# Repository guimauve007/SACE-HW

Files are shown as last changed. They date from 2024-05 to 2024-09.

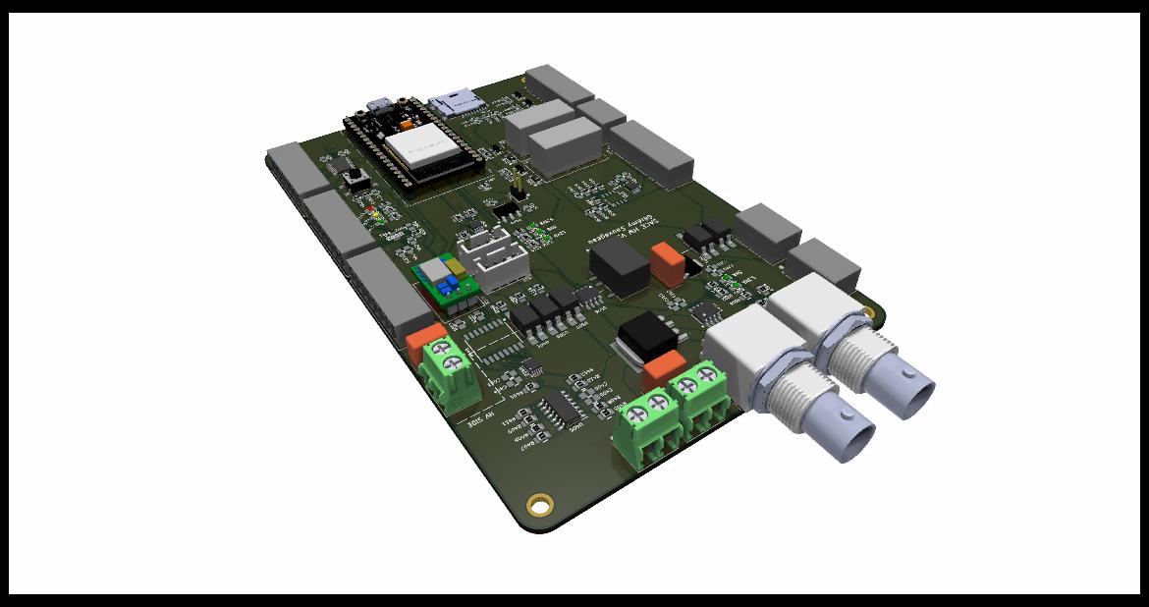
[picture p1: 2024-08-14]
carte_controle/V1/assets/SACE-HW(2).jpg

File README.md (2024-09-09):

# SACE-HW
Répertoire contenant 2 cartes pour machine SACE:

## Getting started
- Installer la dernière version de KiCad ici: https://www.kicad.org/download/
- Cloner ce répertoire sur votre ordinateur local:

```
git clone https://github.com/guimauve007/SACE-HW.git
```

## carte_controle (V1)
Module de contrôle versatile avec les fonctionnalités suivantes:
- 2 connecteurs BNC pour lecture de tension & de courant des électrodes (à l'oscilloscope)
- 8 GPIO/ADC 12 bits 5V
- 2 sorties 0-5V analog (DAC)
- 2 sorties 0-10V analog (DAC)
- 8 sorties 5V haute vitesse (pour stepper drive)
- 2 relais NO 125VAC-10Amp
- 4 Mosfet Open Drain pour load 12V 5.7Amp Max
- Lecture de tension + courant des électrodes jusqu'à 200kSPS avec résolution 12 bits
- Possibilité d'enregistrer un log de données via carte SD
- Interface web utilisateur avec communication MQTT via ESP32
- Connecteurs I2C (x2) pour accessoires auxiliaires  

## interface_piezzos (V1)
- Amplificateur de signal via OP-Amp en mode comparateur (sortie 0-5V)

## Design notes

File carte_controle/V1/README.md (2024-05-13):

# SACE-HW

Répertoire HW du module d'acquisition et d'alimentation de la SACE hybride 3 axes

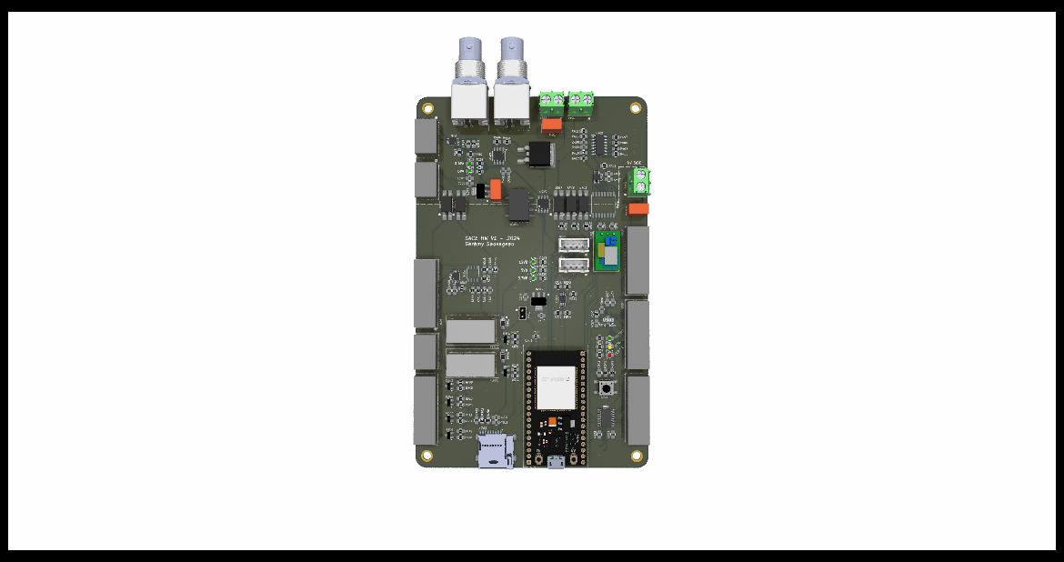
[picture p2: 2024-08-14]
carte_controle/V1/assets/SACE-HW.jpg

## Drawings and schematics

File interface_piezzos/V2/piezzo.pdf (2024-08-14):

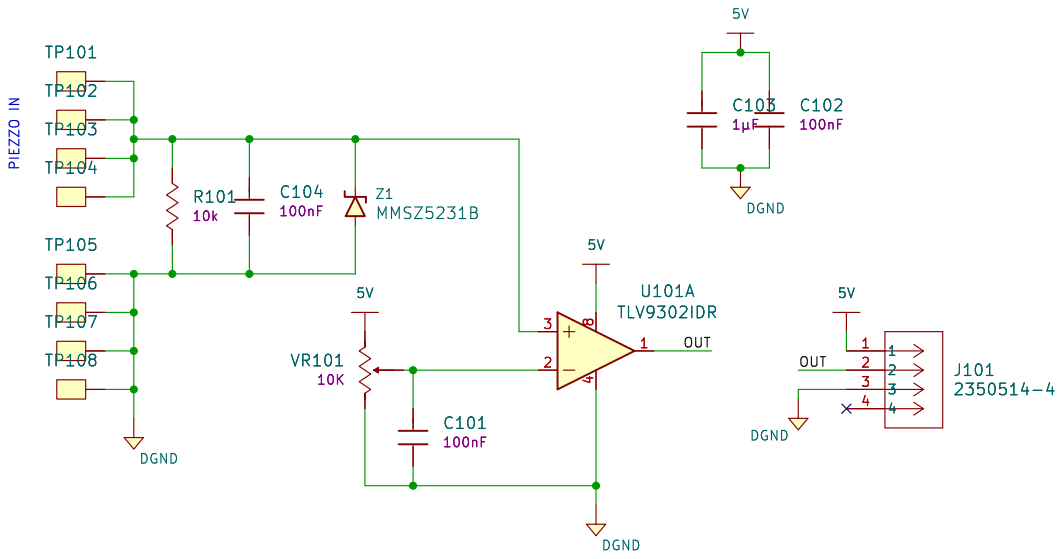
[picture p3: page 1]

File: piezzo.kicad_sch Sheet: / þÿGérémy Sauvageau

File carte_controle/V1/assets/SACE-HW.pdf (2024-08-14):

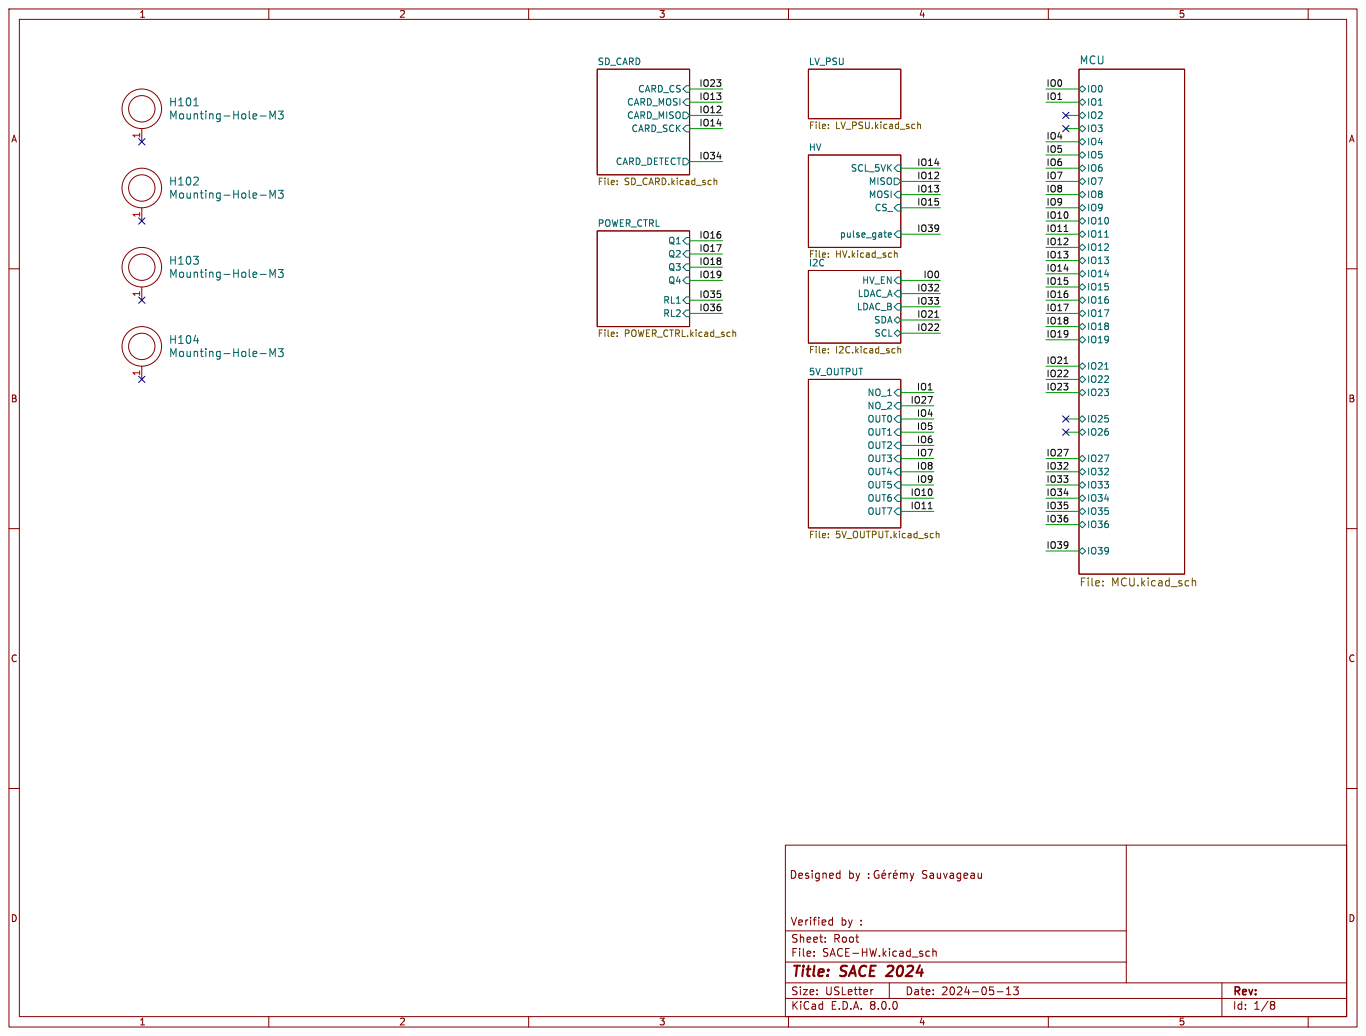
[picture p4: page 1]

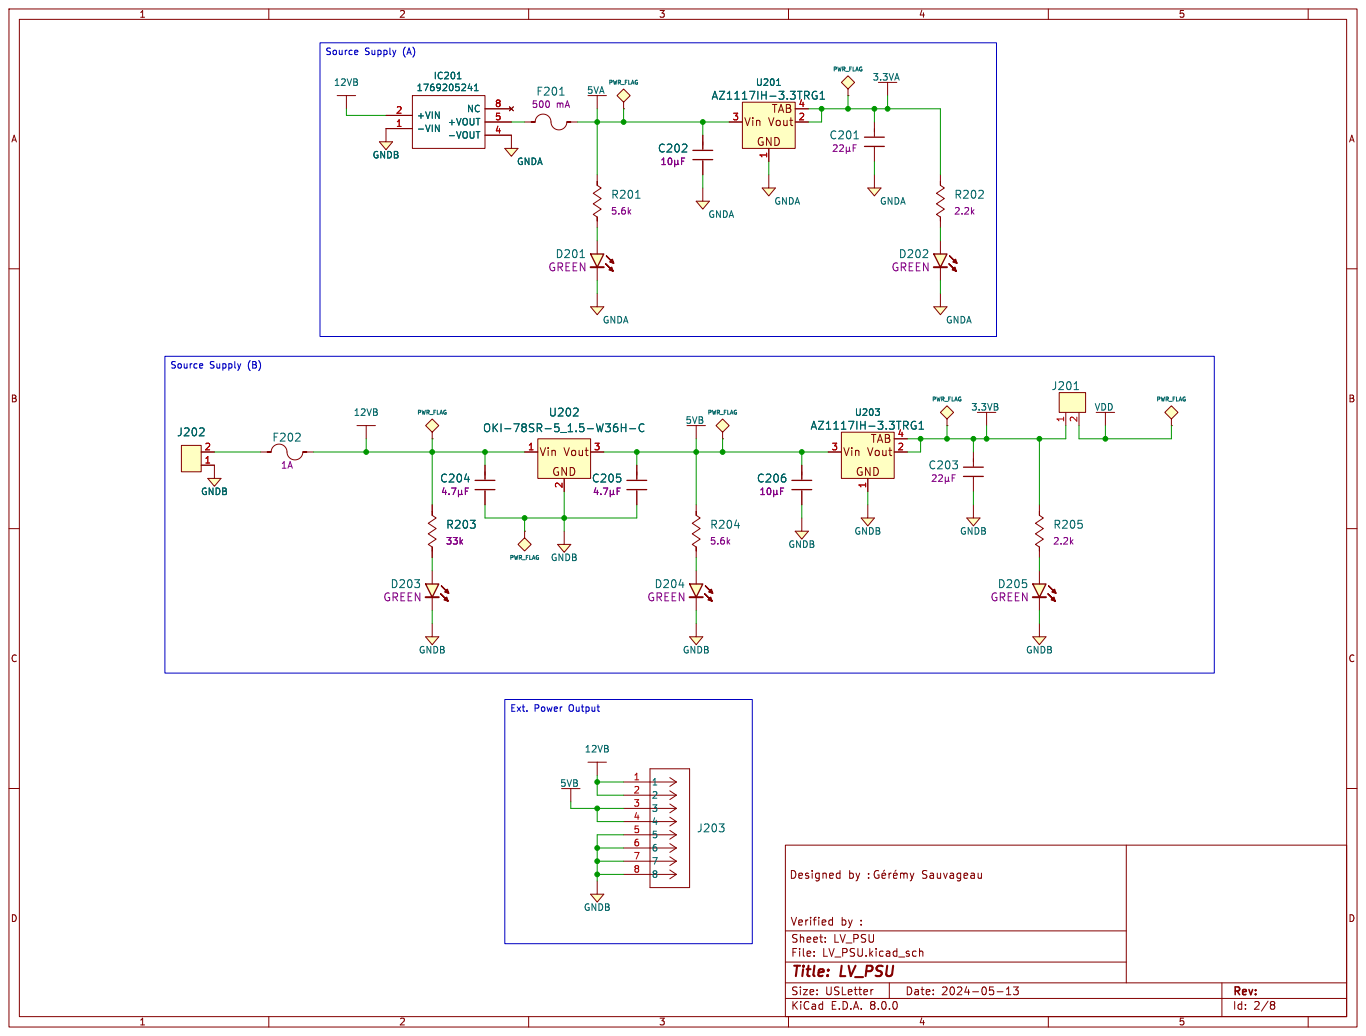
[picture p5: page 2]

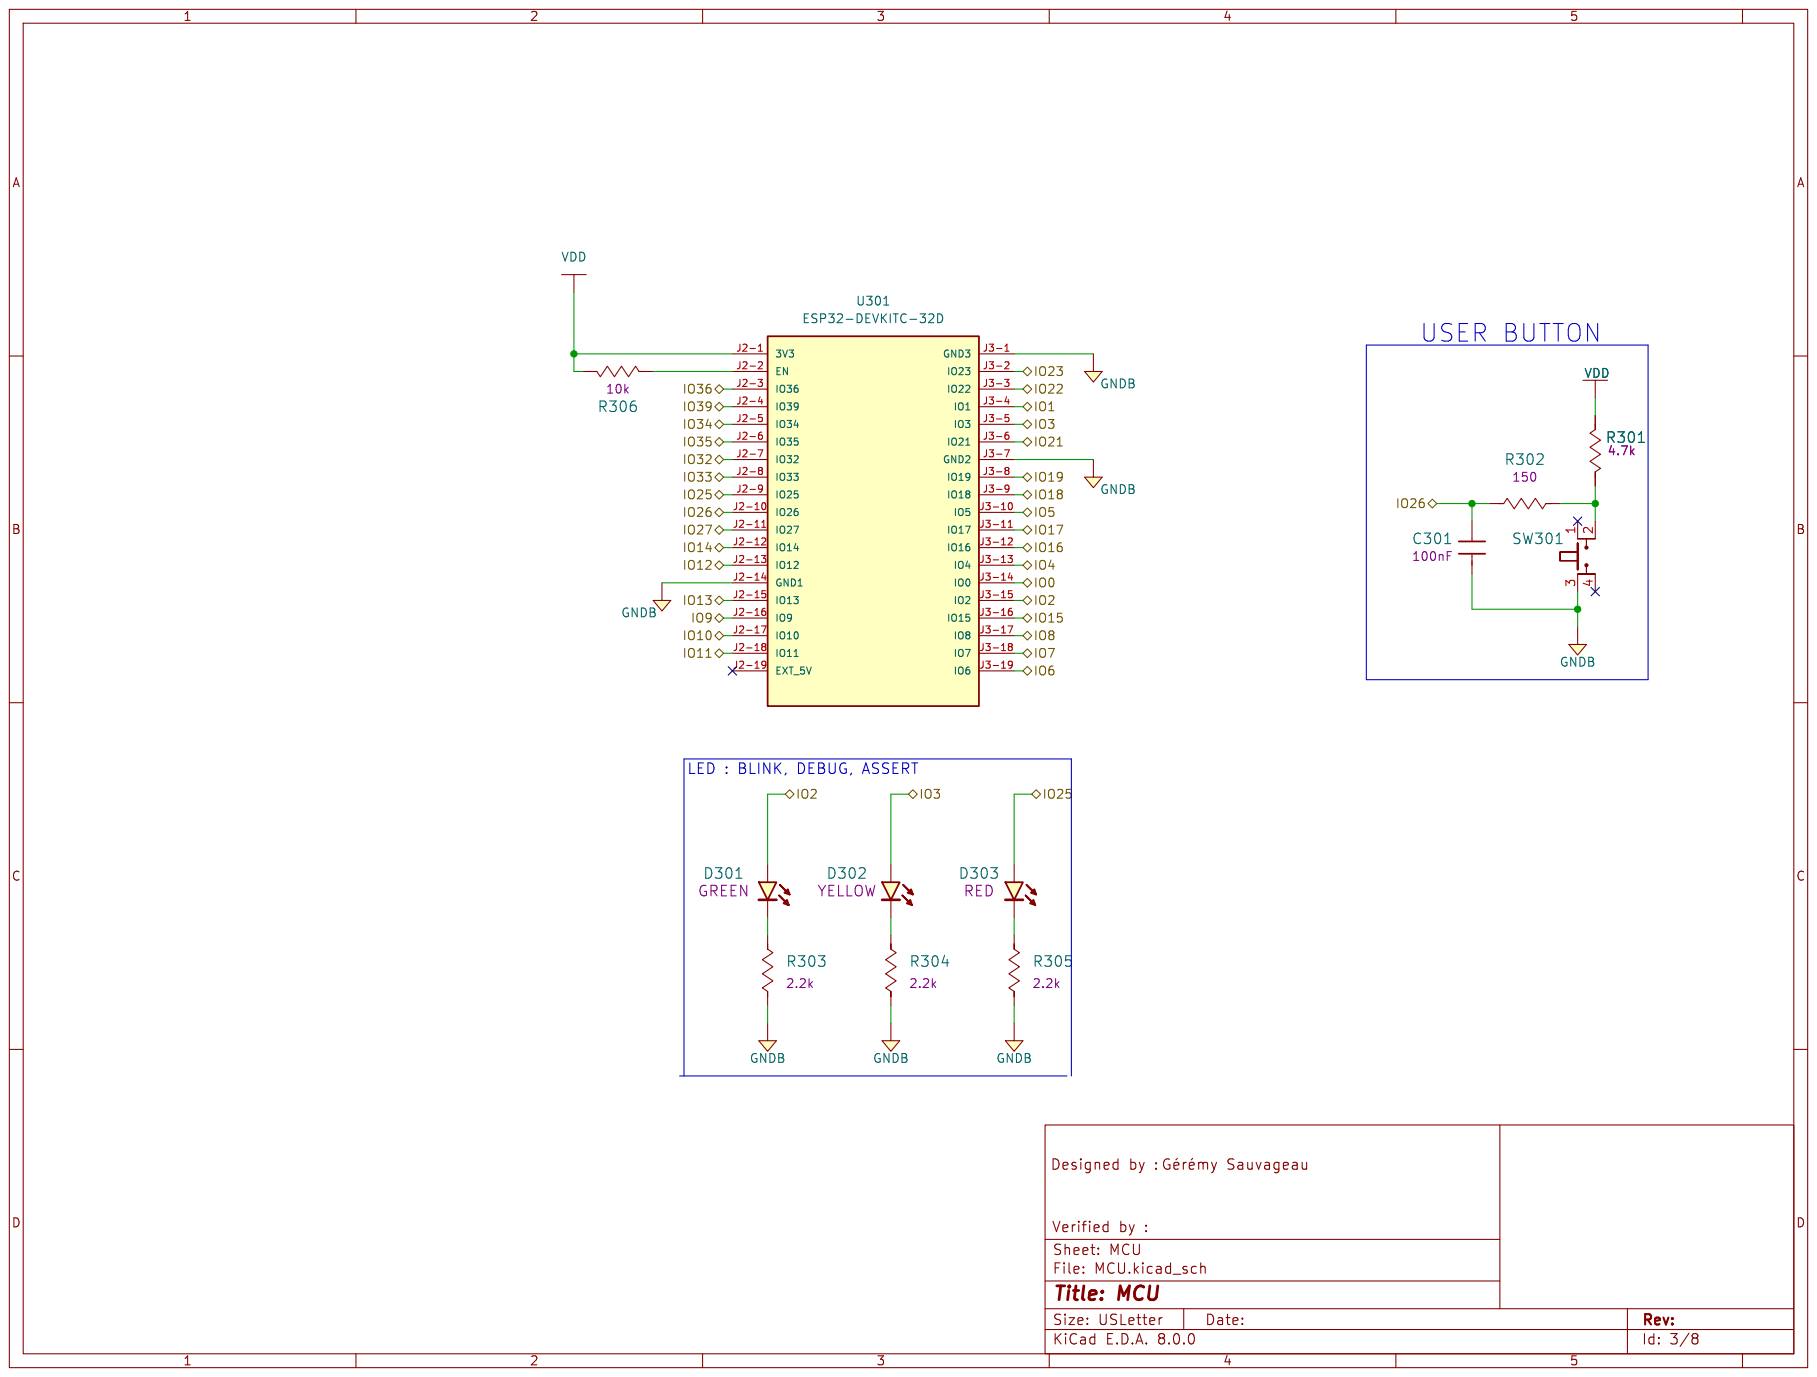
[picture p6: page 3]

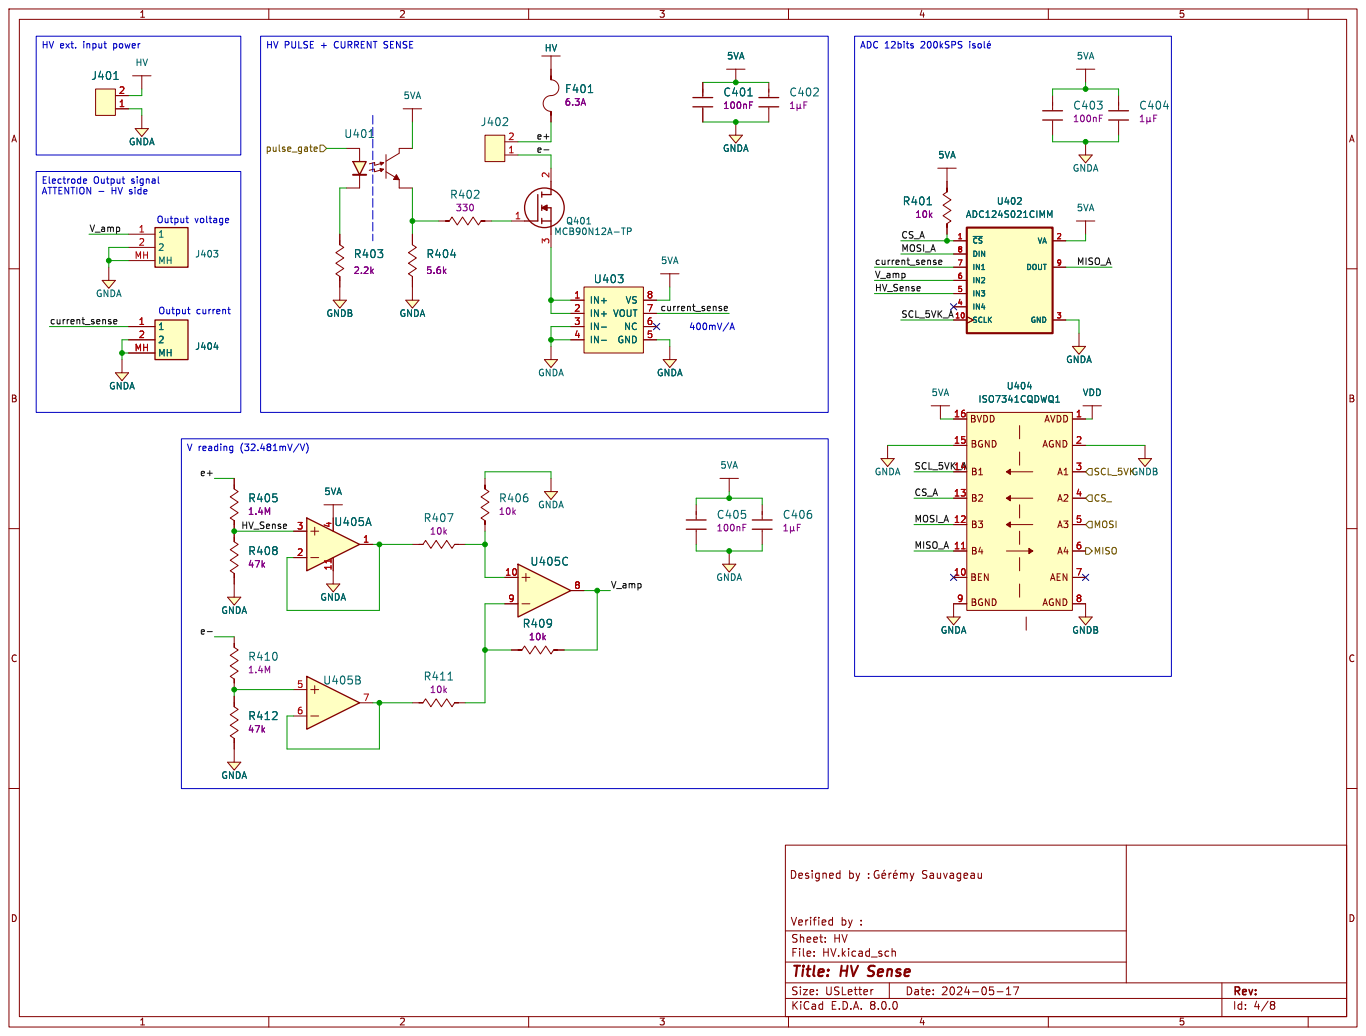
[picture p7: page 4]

Id: 4/8 Title: HV Sense

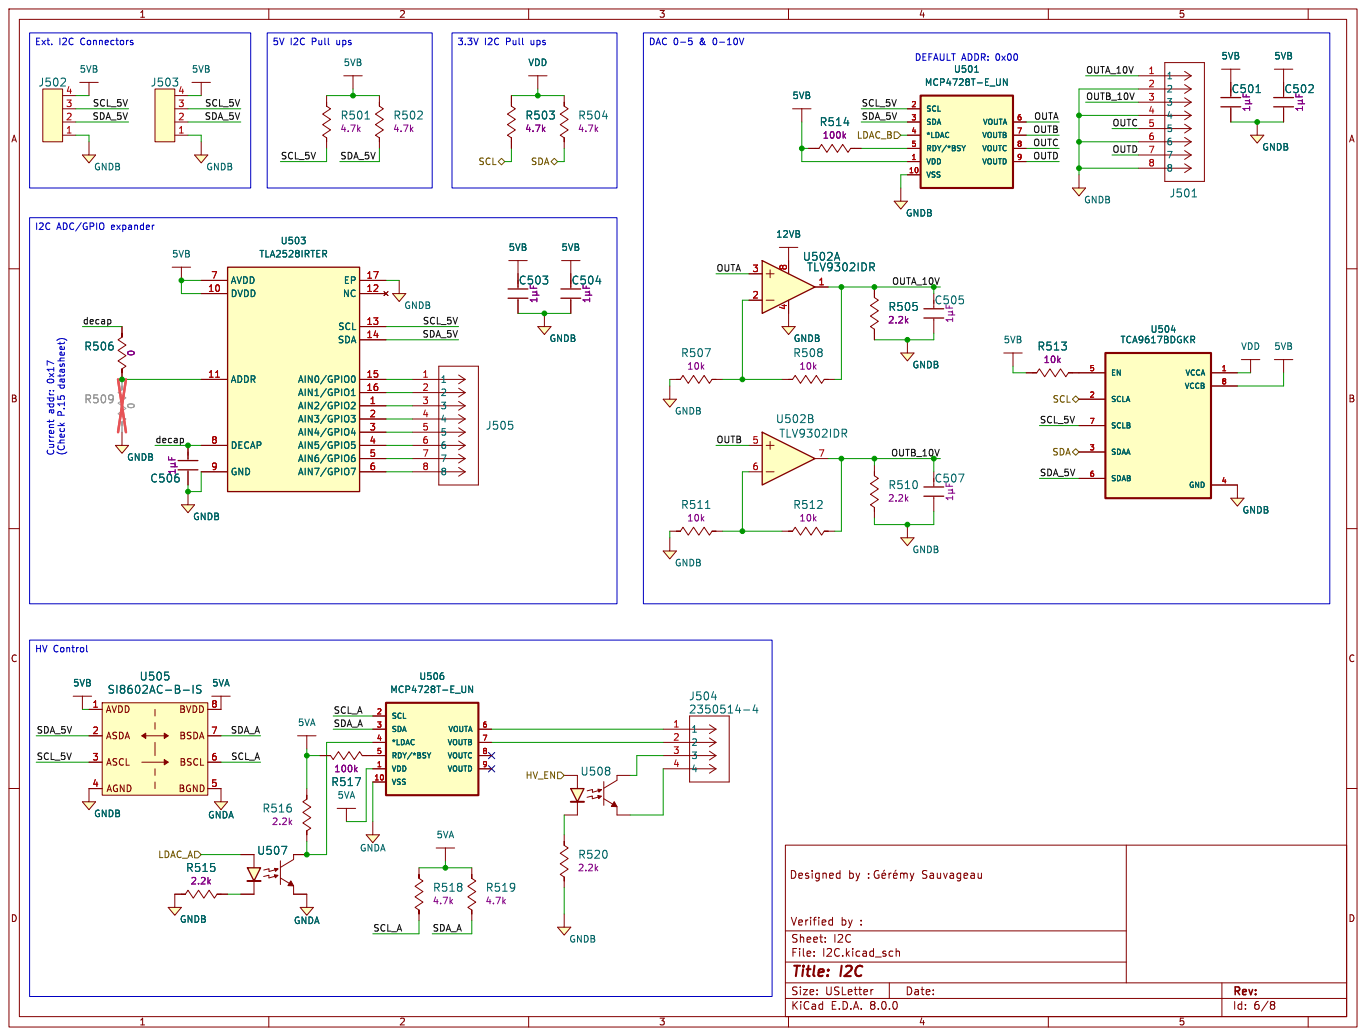
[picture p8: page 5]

I2C ADC/GPIO expander HV Control

SDA_5V Current addr: 0x17 (Check P.15 datasheet)

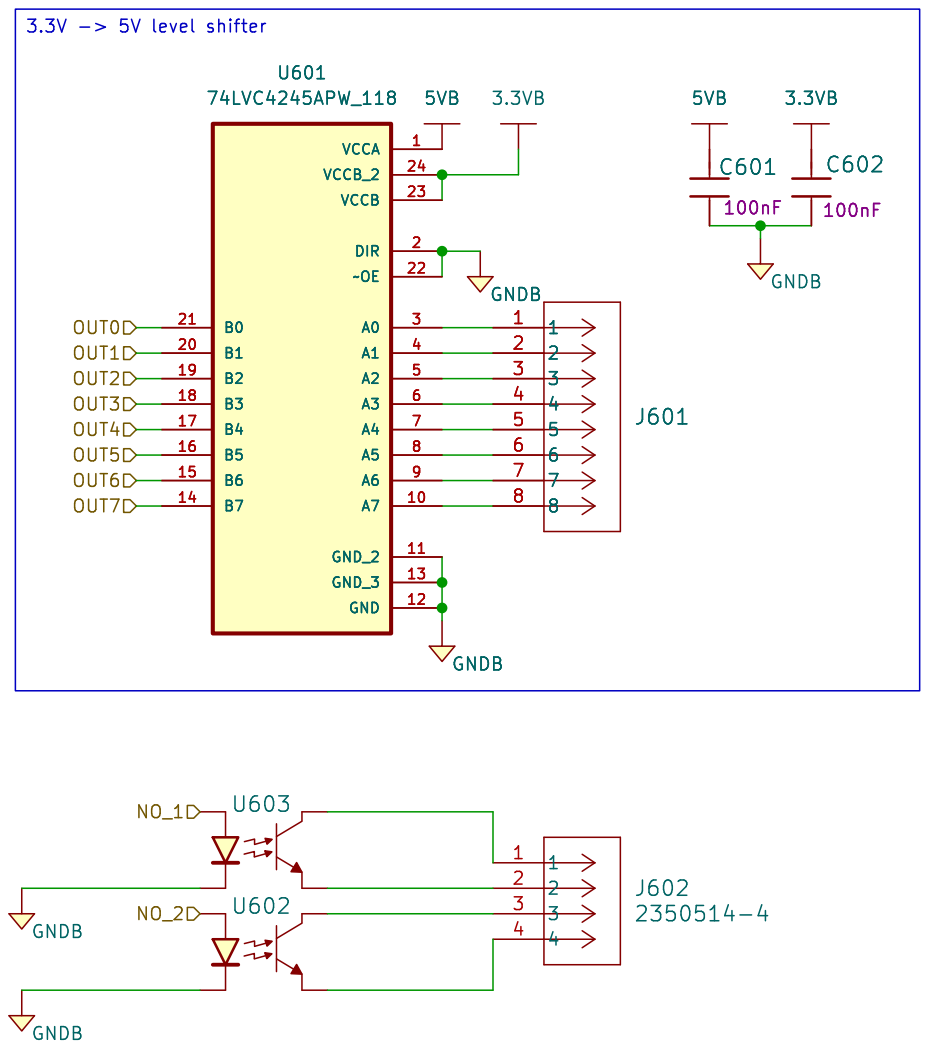
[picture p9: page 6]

Id: 7/8 Title: 5V Output File: 5V_OUTPUT.kicad_sch Sheet: 5V_OUTPUT

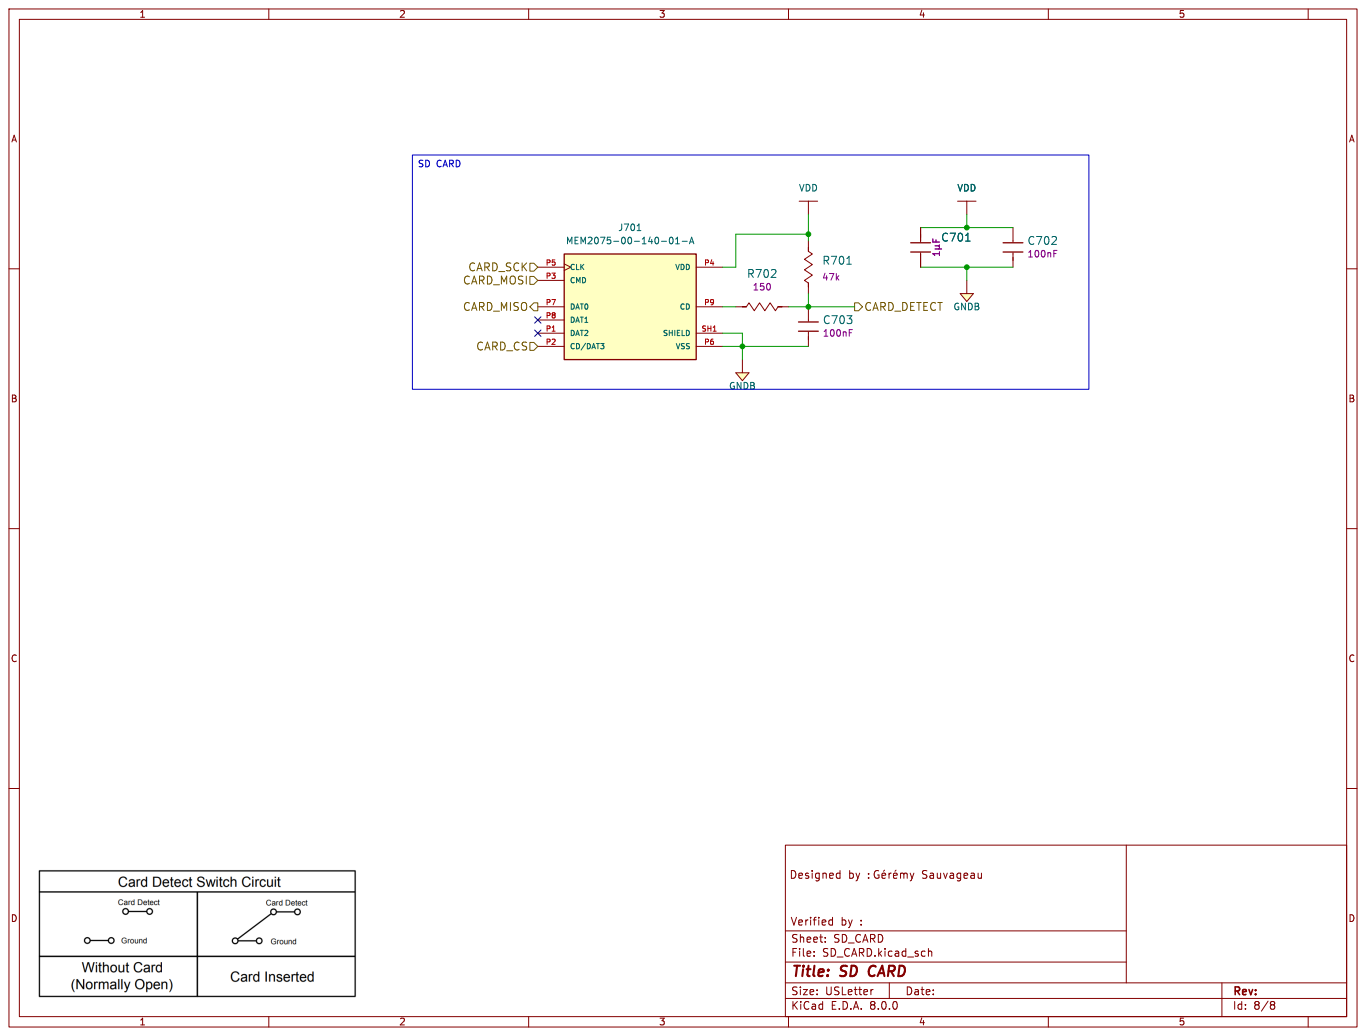
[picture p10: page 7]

File: SD_CARD.kicad_sch Sheet: SD_CARD
Id: 8/8 Title: SD CARD

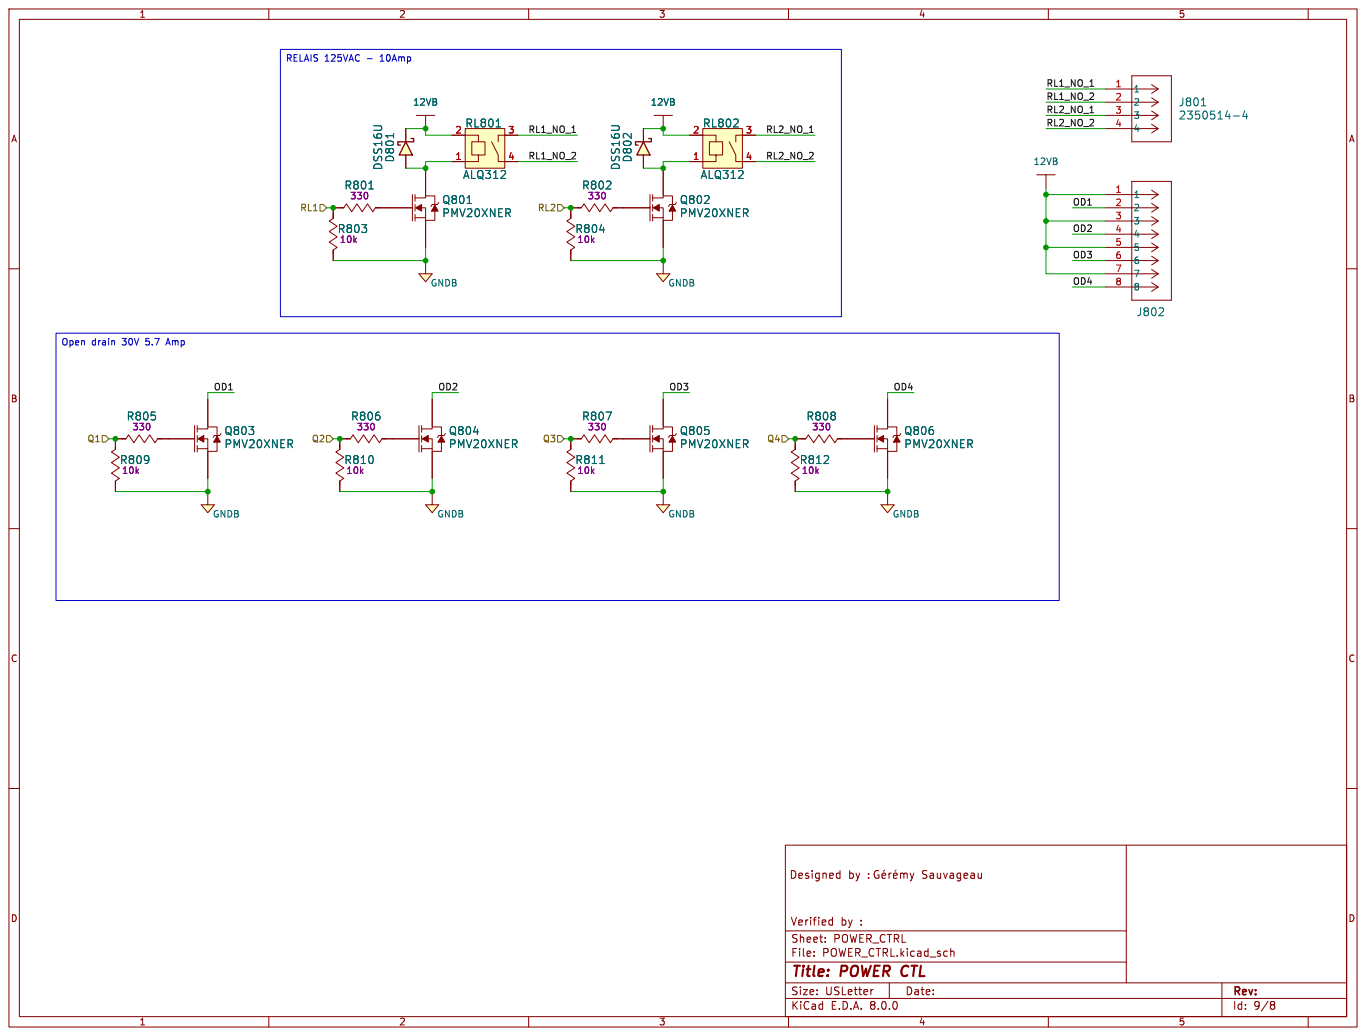
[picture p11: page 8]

Id: 9/8 Title: POWER CTL

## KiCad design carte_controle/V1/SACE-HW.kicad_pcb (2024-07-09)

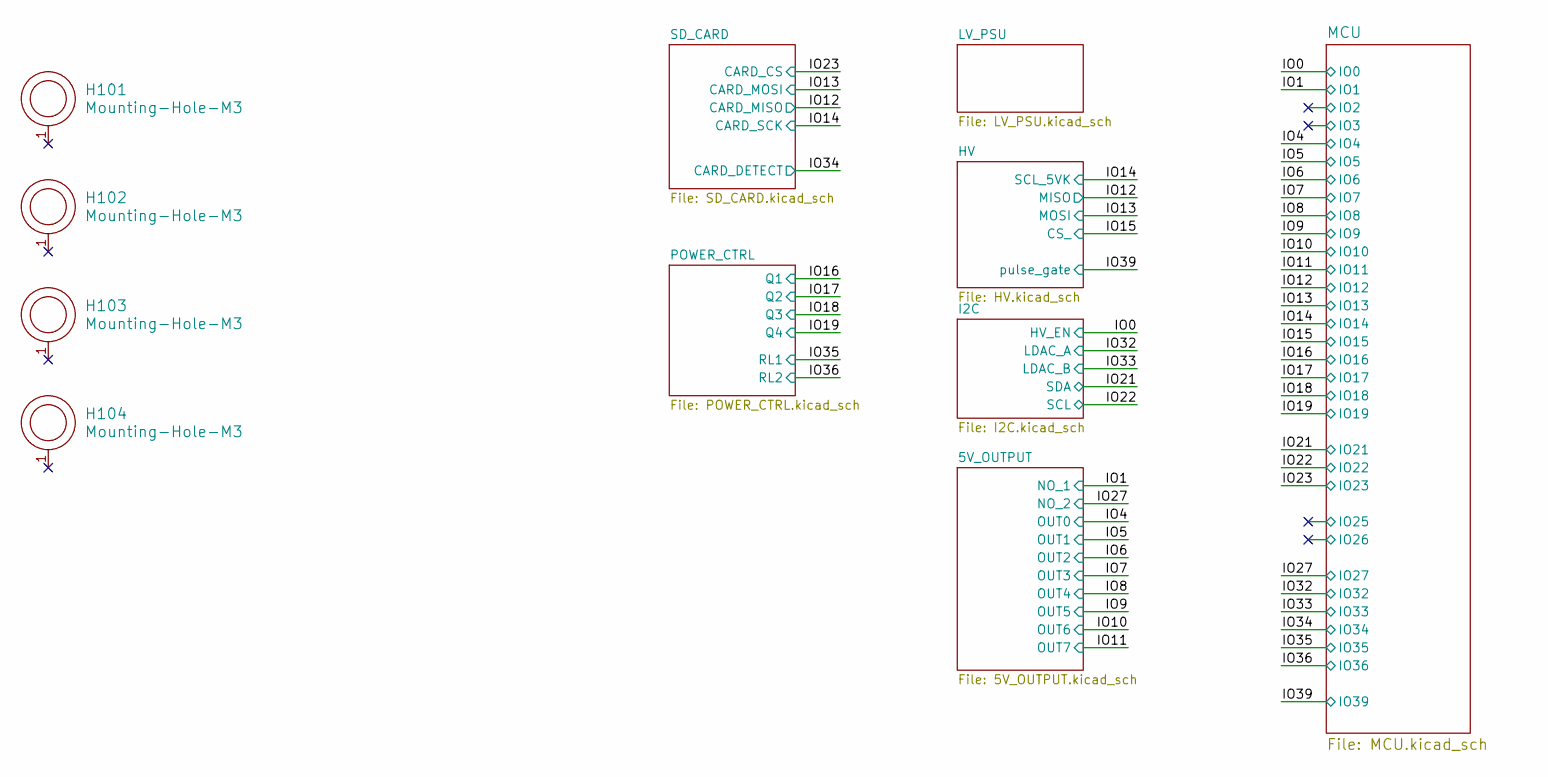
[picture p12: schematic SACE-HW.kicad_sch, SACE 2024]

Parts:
H101, H102, H103, H104: Mounting-Hole-M3; Mounting_Hole_3mm

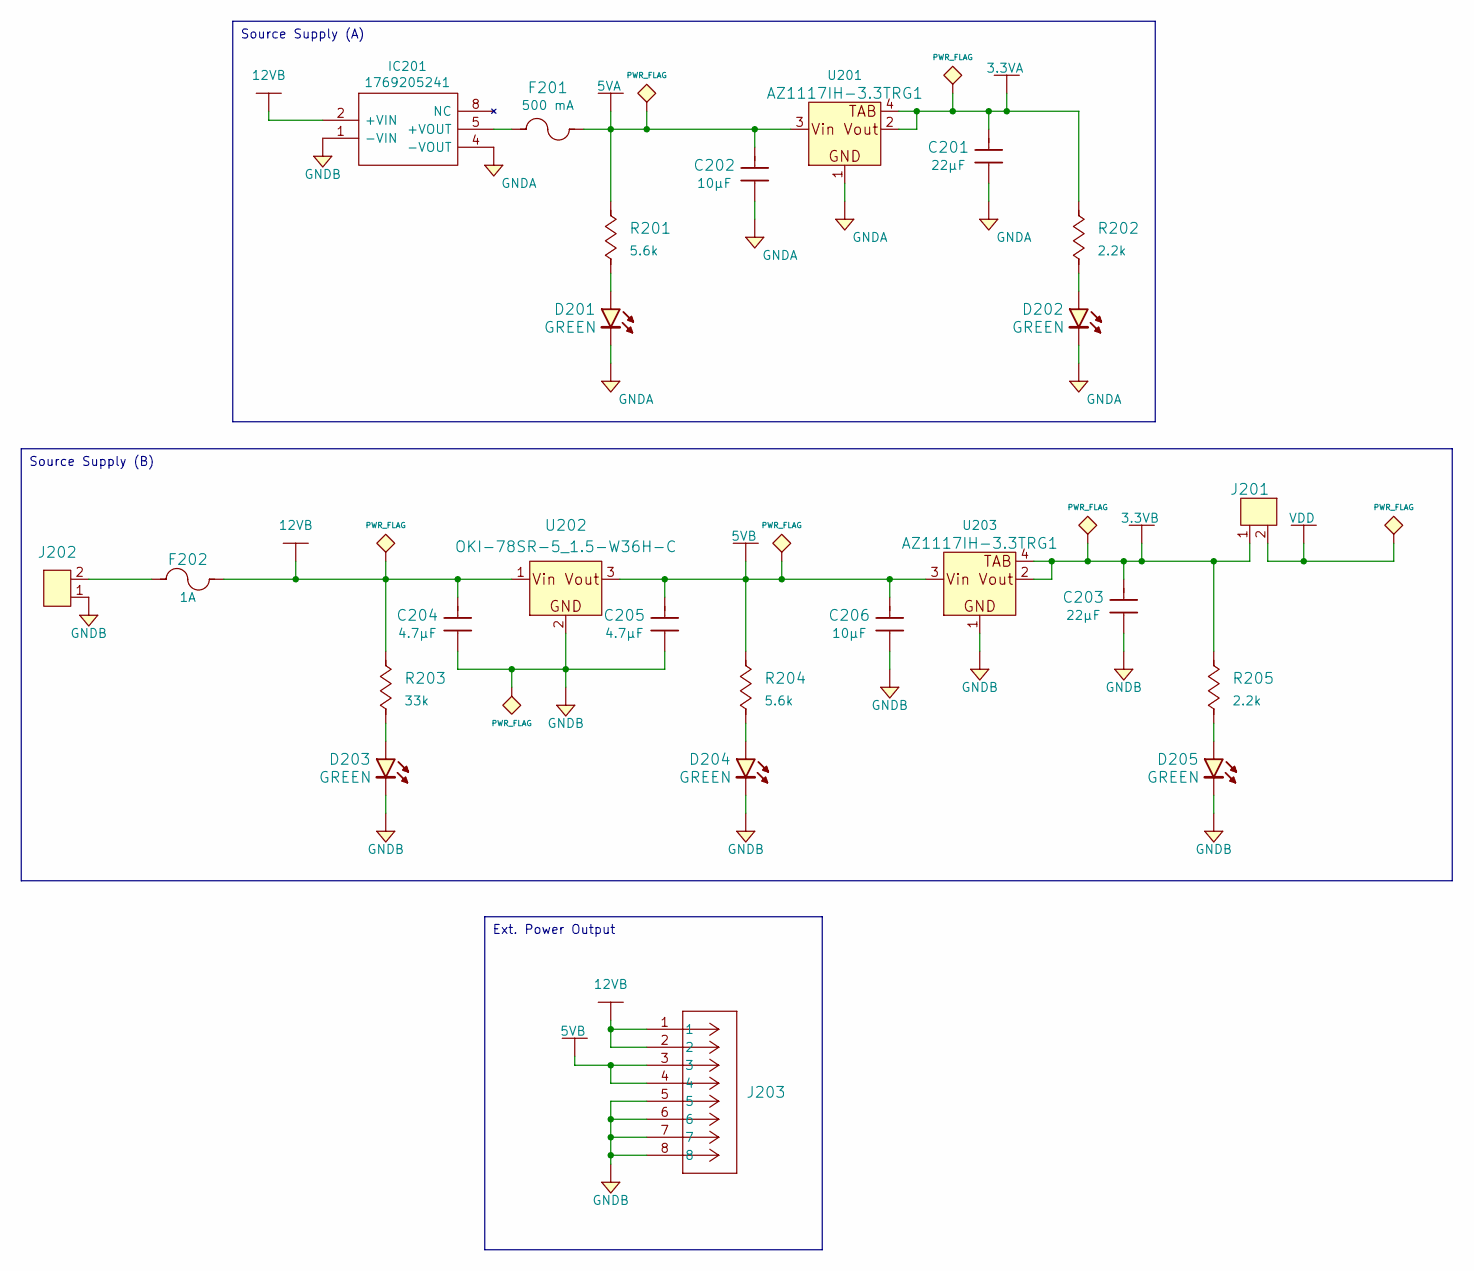
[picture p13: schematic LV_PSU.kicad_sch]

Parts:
C201, C203: 885012107005; C0805; Tolerance (%) ±20%; Voltage Rated (Volt) 6.3V; Manufacturer Part Number 885012107005
C202, C206: 885012107014; C0805; Tolerance (%) ±20%; Voltage Rated (Volt) 16V; Manufacturer Part Number 885012007027
C204, C205: 885012107018; C0805; Tolerance (%) ±20%; Voltage Rated (Volt) 25V; Manufacturer Part Number 885012107018
D201, D202, D203, D204, D205: 150080VS75000; LED_0805_GREEN; Voltage - Forward (Vf) 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 2V; Manufacturer Part Number 150080VS75000
F201: 39511000440; TE5_395; Current Rating (A) 500 mA; Voltage Rating - AC 125V; Manufacturer Part Number 56200001009
F202: 39511000440; TE5_395; Current Rating (A) 1A; Voltage Rating - AC 125V; Manufacturer Part Number 39511000440
IC201: 1769205241; Voltage - Input (Min) 4.5V; Voltage - Input (Max) 36V; Manufacturer Part Number 1769205241; Mouser Part Number 710-1769205241
J201: Header_Male_Pin_2.54mm_1X2_,_Unshrouded; Headers_2.54mm_1X2; Manufacturer Part Number Manufacturer Part Number
J202: 1935161; Manufacturer Part Number 1935161
J203: 2350514-8; CONN8_2350514-8_TEC; Manufacturer Part Number 2350514-8
R201, R204: RC0805FR-075K6L; R0805; Tolerance (%) ±1%; Manufacturer Part Number RC0805FR-075K6L
R202, R205: RC0805JR-072K2L; R0805; Tolerance (%) ±5%; Manufacturer Part Number RC0805JR-072K2L
R203: RC0805JR-0733KL; R0805; Tolerance (%) ±5%; Manufacturer Part Number RC0805JR-0733KL
U201, U203: AZ1117IH-3.3TRG1; SOT-223-3; Voltage - Output 3.3V; Voltage - Dropout (Typi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 1.2V @ 800mA; Manufacturer Part Number AZ1117IH-3.3TRG1
U202: OKI-78SR-5_1.5-W36H-C; OKI-78SR_Horizontal; Voltage - Input (Min) 7V; Voltage - Input (Max) 36V; Manufacturer Part Number OKI-78SR-5/1.5-W36H-C

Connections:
3.3VA: C201.2, R202.2, U201.2 (Vout), U201.4 (Vout_(TAB))
3.3VB: C203.2, J201.1, R205.2, U203.2 (Vout), U203.4 (Vout_(TAB)); also elsewhere on the board
5VA: C202.2, F201.2, R201.2, U201.3 (Vin); also elsewhere on the board
5VB: C205.2, C206.2, J203.3, J203.4, R204.2, U202.3 (Vout), U203.3 (Vin); also elsewhere on the board
12VB: C204.2, F202.2, IC201.2 (+VIN), J203.1, J203.2, R203.2, U202.1 (Vin); also elsewhere on the board
GNDA: C201.1, C202.1, D201.1 (Cathode), D202.1 (Cathode), IC201.4 (-VOUT), U201.1 (GND); also elsewhere on the board
GNDB: C203.1, C204.1, C205.1, C206.1, D203.1 (Cathode), D204.1 (Cathode), D205.1 (Cathode), IC201.1 (-VIN), J202.1, J203.5, J203.6, J203.7, J203.8, U202.2 (GND), U203.1 (GND); also elsewhere on the board
unnamed: D201.2 (Anode), R201.1
unnamed: D202.2 (Anode), R202.1
unnamed: D203.2 (Anode), R203.1
unnamed: D204.2 (Anode), R204.1
unnamed: D205.2 (Anode), R205.1
unnamed: F202.1, J202.2
unnamed: F201.1, IC201.5 (+VOUT)
VDD: J201.2; also elsewhere on the board

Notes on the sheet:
Source Supply (A)
Source Supply (B)
Ext. Power Output

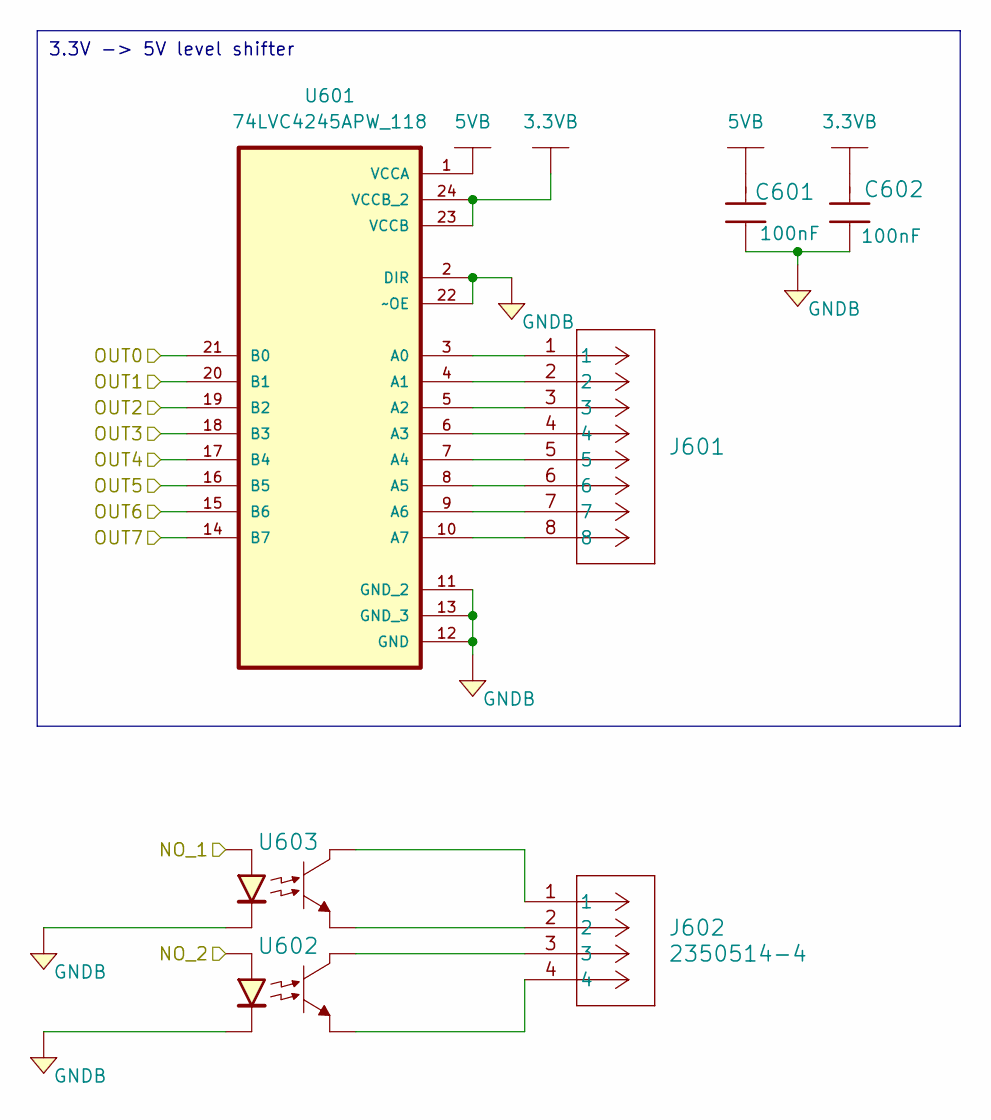
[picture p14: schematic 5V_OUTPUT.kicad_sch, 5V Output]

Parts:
C601, C602: 885012207098; C0805; Tolerance (%) ±10%; Voltage Rated (Volt) 50V; Manufacturer Part Number 885012207098
J601: 2350514-8; CONN8_2350514-8_TEC; Manufacturer Part Number 2350514-8
J602: 2350514-4; CONN4_1155650000_TEC; Manufacturer Part Number 2350514-4
U601: 74LVC4245APW_118; SOP65P640X110-24N; Manufacturer Part Number 74LVC4245APW_118
U602, U603: LTV-816S; 4-SMD; Manufacturer Part Number LTV-816S

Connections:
3.3VB: C602.2, U601.23 (VCCB), U601.24 (VCCB_2); also elsewhere on the board
5VB: C601.2, U601.1 (VCCA); also elsewhere on the board
/IO1: U603.1 (Anode); also elsewhere on the board
/IO4: U601.21 (B0); also elsewhere on the board
/IO5: U601.20 (B1); also elsewhere on the board
/IO6: U601.19 (B2); also elsewhere on the board
/IO7: U601.18 (B3); also elsewhere on the board
/IO8: U601.17 (B4); also elsewhere on the board
/IO9: U601.16 (B5); also elsewhere on the board
/IO10: U601.15 (B6); also elsewhere on the board
/IO11: U601.14 (B7); also elsewhere on the board
/IO27: U602.1 (Anode); also elsewhere on the board
GNDB: C601.1, C602.1, U601.2 (DIR), U601.11 (GND_2), U601.12 (GND), U601.13 (GND_3), U601.22 (~OE), U602.2 (Cathode), U603.2 (Cathode); also elsewhere on the board
unnamed: J601.1, U601.3 (A0)
unnamed: J601.2, U601.4 (A1)
unnamed: J601.3, U601.5 (A2)
unnamed: J601.4, U601.6 (A3)
unnamed: J601.5, U601.7 (A4)
unnamed: J601.6, U601.8 (A5)
unnamed: J601.7, U601.9 (A6)
unnamed: J601.8, U601.10 (A7)
unnamed: J602.3, U602.4 (C)
unnamed: J602.4, U602.3 (E)
unnamed: J602.1, U603.4 (C)
unnamed: J602.2, U603.3 (E)

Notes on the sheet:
3.3V -> 5V level shifter

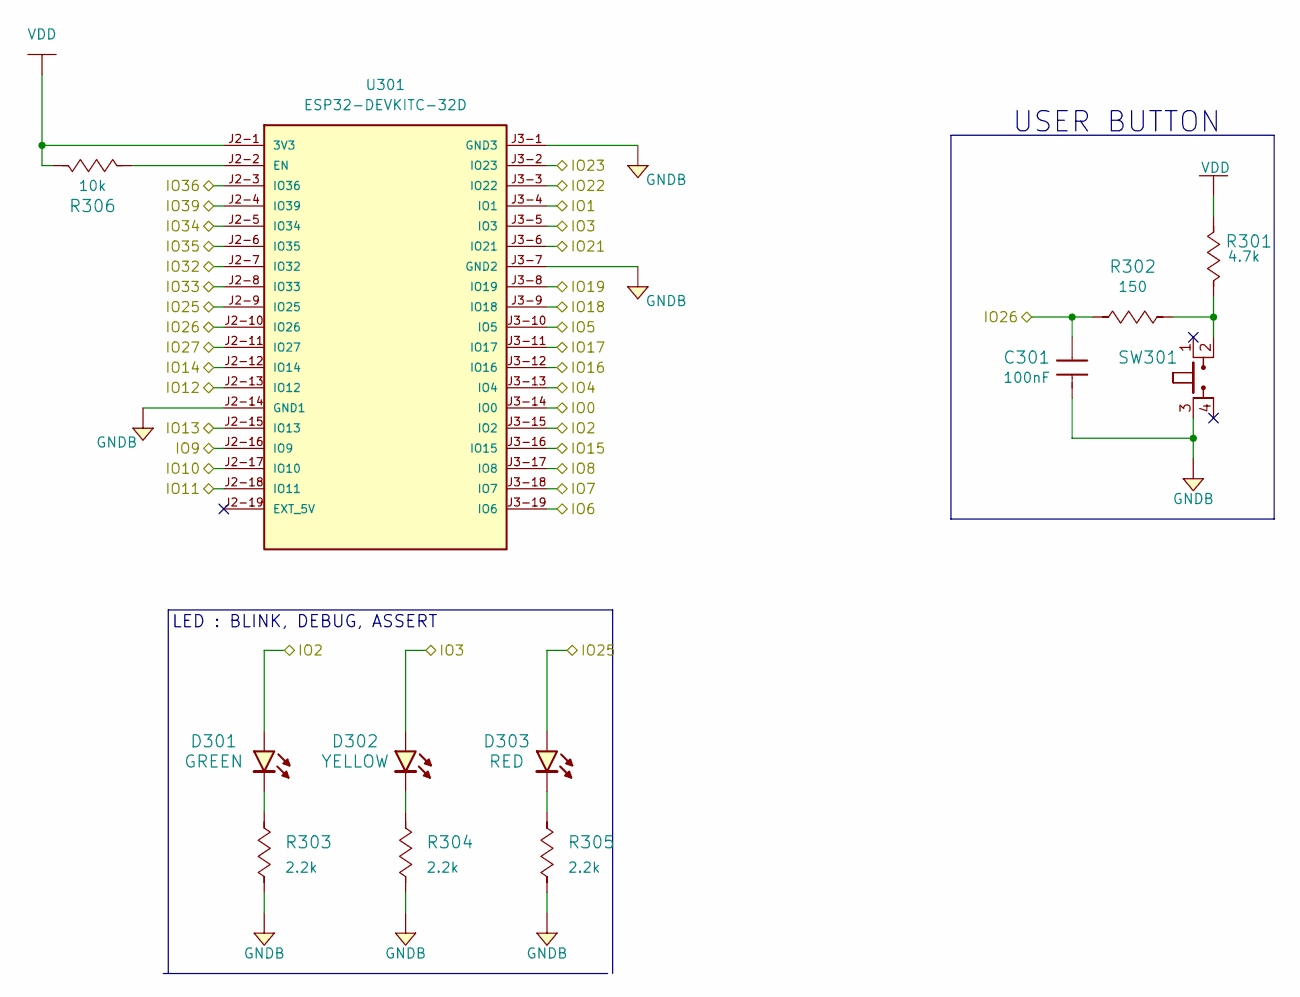
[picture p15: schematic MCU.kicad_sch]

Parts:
C301: 885012207098; C0805; Tolerance (%) ±10%; Voltage Rated (Volt) 50V; Manufacturer Part Number 885012207098
D301: 150080VS75000; LED_0805_GREEN; Voltage - Forward (Vf) 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 2V; Manufacturer Part Number 150080VS75000
D302: 150080YS75000; LED_0805_YELLOW; Voltage - Forward (Vf) 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 2V; Manufacturer Part Number 150080YS75000
D303: 150080RS75000; LED_0805_RED; Voltage - Forward (Vf) 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 2V; Manufacturer Part Number 150080RS75000
R301: RC0805JR-074K7L; R0805; Tolerance (%) ±5%; Manufacturer Part Number RC0805JR-074K7L
R302: RC0805JR-07150RL; R0805; Tolerance (%) ±5%; Manufacturer Part Number RC0805JR-07150RL
R303, R304, R305: RC0805JR-072K2L; R0805; Tolerance (%) ±5%; Manufacturer Part Number RC0805JR-072K2L
R306: RC0805JR-0710KL; R0805; Tolerance (%) ±5%; Manufacturer Part Number RC0805JR-0710KL
SW301: PTS645SM43SMTR92; PTS645_6X6X4_SMD; Manufacturer Part Number PTS645SM43SMTR92 LFS
U301: ESP32-DEVKITC-32D; MODULE_ESP32-DEVKITC-32D; PARTREV V4

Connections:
/IO0: U301.J3-14 (IO0); also elsewhere on the board
/IO1: U301.J3-4 (IO1); also elsewhere on the board
/IO4: U301.J3-13 (IO4); also elsewhere on the board
/IO5: U301.J3-10 (IO5); also elsewhere on the board
/IO6: U301.J3-19 (IO6); also elsewhere on the board
/IO7: U301.J3-18 (IO7); also elsewhere on the board
/IO8: U301.J3-17 (IO8); also elsewhere on the board
/IO9: U301.J2-16 (IO9); also elsewhere on the board
/IO10: U301.J2-17 (IO10); also elsewhere on the board
/IO11: U301.J2-18 (IO11); also elsewhere on the board
/IO12: U301.J2-13 (IO12); also elsewhere on the board
/IO13: U301.J2-15 (IO13); also elsewhere on the board
/IO14: U301.J2-12 (IO14); also elsewhere on the board
/IO15: U301.J3-16 (IO15); also elsewhere on the board
/IO16: U301.J3-12 (IO16); also elsewhere on the board
/IO17: U301.J3-11 (IO17); also elsewhere on the board
/IO18: U301.J3-9 (IO18); also elsewhere on the board
/IO19: U301.J3-8 (IO19); also elsewhere on the board
/IO21: U301.J3-6 (IO21); also elsewhere on the board
/IO22: U301.J3-3 (IO22); also elsewhere on the board
/IO23: U301.J3-2 (IO23); also elsewhere on the board
/IO27: U301.J2-11 (IO27); also elsewhere on the board
/IO32: U301.J2-7 (IO32); also elsewhere on the board
/IO33: U301.J2-8 (IO33); also elsewhere on the board
/IO34: U301.J2-5 (IO34); also elsewhere on the board
/IO35: U301.J2-6 (IO35); also elsewhere on the board
/IO36: U301.J2-3 (IO36); also elsewhere on the board
/IO39: U301.J2-4 (IO39); also elsewhere on the board
/MCU/IO2: D301.2 (Anode), U301.J3-15 (IO2)
/MCU/IO3: D302.2 (Anode), U301.J3-5 (IO3)
/MCU/IO25: D303.2 (Anode), U301.J2-9 (IO25)
/MCU/IO26: C301.1, R302.1, U301.J2-10 (IO26)
GNDB: C301.2, R303.1, R304.1, R305.1, SW301.3, U301.J2-14 (GND1), U301.J3-1 (GND3), U301.J3-7 (GND2); also elsewhere on the board
unnamed: D301.1 (Cathode), R303.2
unnamed: D302.1 (Cathode), R304.2
unnamed: D303.1 (Cathode), R305.2
unnamed: R301.1, R302.2, SW301.2
unnamed: R306.2, U301.J2-2 (EN)
VDD: R301.2, R306.1, U301.J2-1 (3V3); also elsewhere on the board

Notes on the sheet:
LED : BLINK, DEBUG, ASSERT
USER BUTTON

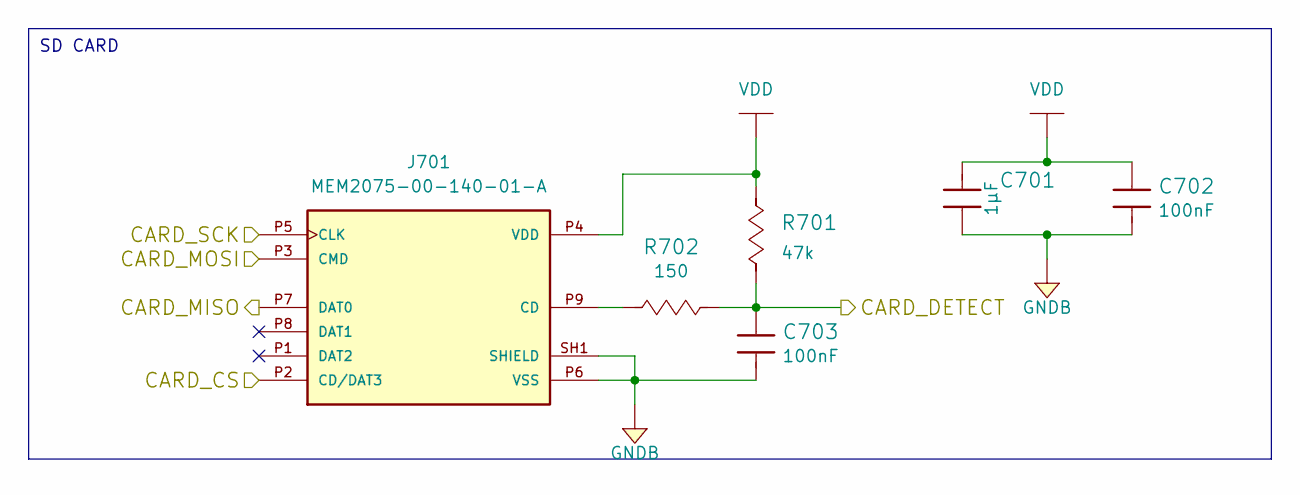
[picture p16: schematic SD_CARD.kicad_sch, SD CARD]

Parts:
C701: 885012107015; C0805; Tolerance (%) ±20%; Voltage Rated (Volt) 25V; Manufacturer Part Number 885012107015
C702, C703: 885012207098; C0805; Tolerance (%) ±10%; Voltage Rated (Volt) 50V; Manufacturer Part Number 885012207098
J701: MEM2075-00-140-01-A; GCT_MEM2075-00-140-01-A; PARTREV A
R701: RC0805FR-0747KL; R0805; Tolerance (%) ±1%; Manufacturer Part Number RC0805FR-0747KL
R702: RC0805JR-07150RL; R0805; Tolerance (%) ±5%; Manufacturer Part Number RC0805JR-07150RL

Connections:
/IO12: J701.P7 (DAT0); also elsewhere on the board
/IO13: J701.P3 (CMD); also elsewhere on the board
/IO14: J701.P5 (CLK); also elsewhere on the board
/IO23: J701.P2 (CD/DAT3); also elsewhere on the board
/IO34: C703.1, R701.1, R702.2; also elsewhere on the board
GNDB: C701.1, C702.2, C703.2, J701.P6 (VSS), J701.SH1 (SHIELD); also elsewhere on the board
unnamed: J701.P9 (CD), R702.1
VDD: C701.2, C702.1, J701.P4 (VDD), R701.2; also elsewhere on the board

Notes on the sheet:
SD CARD

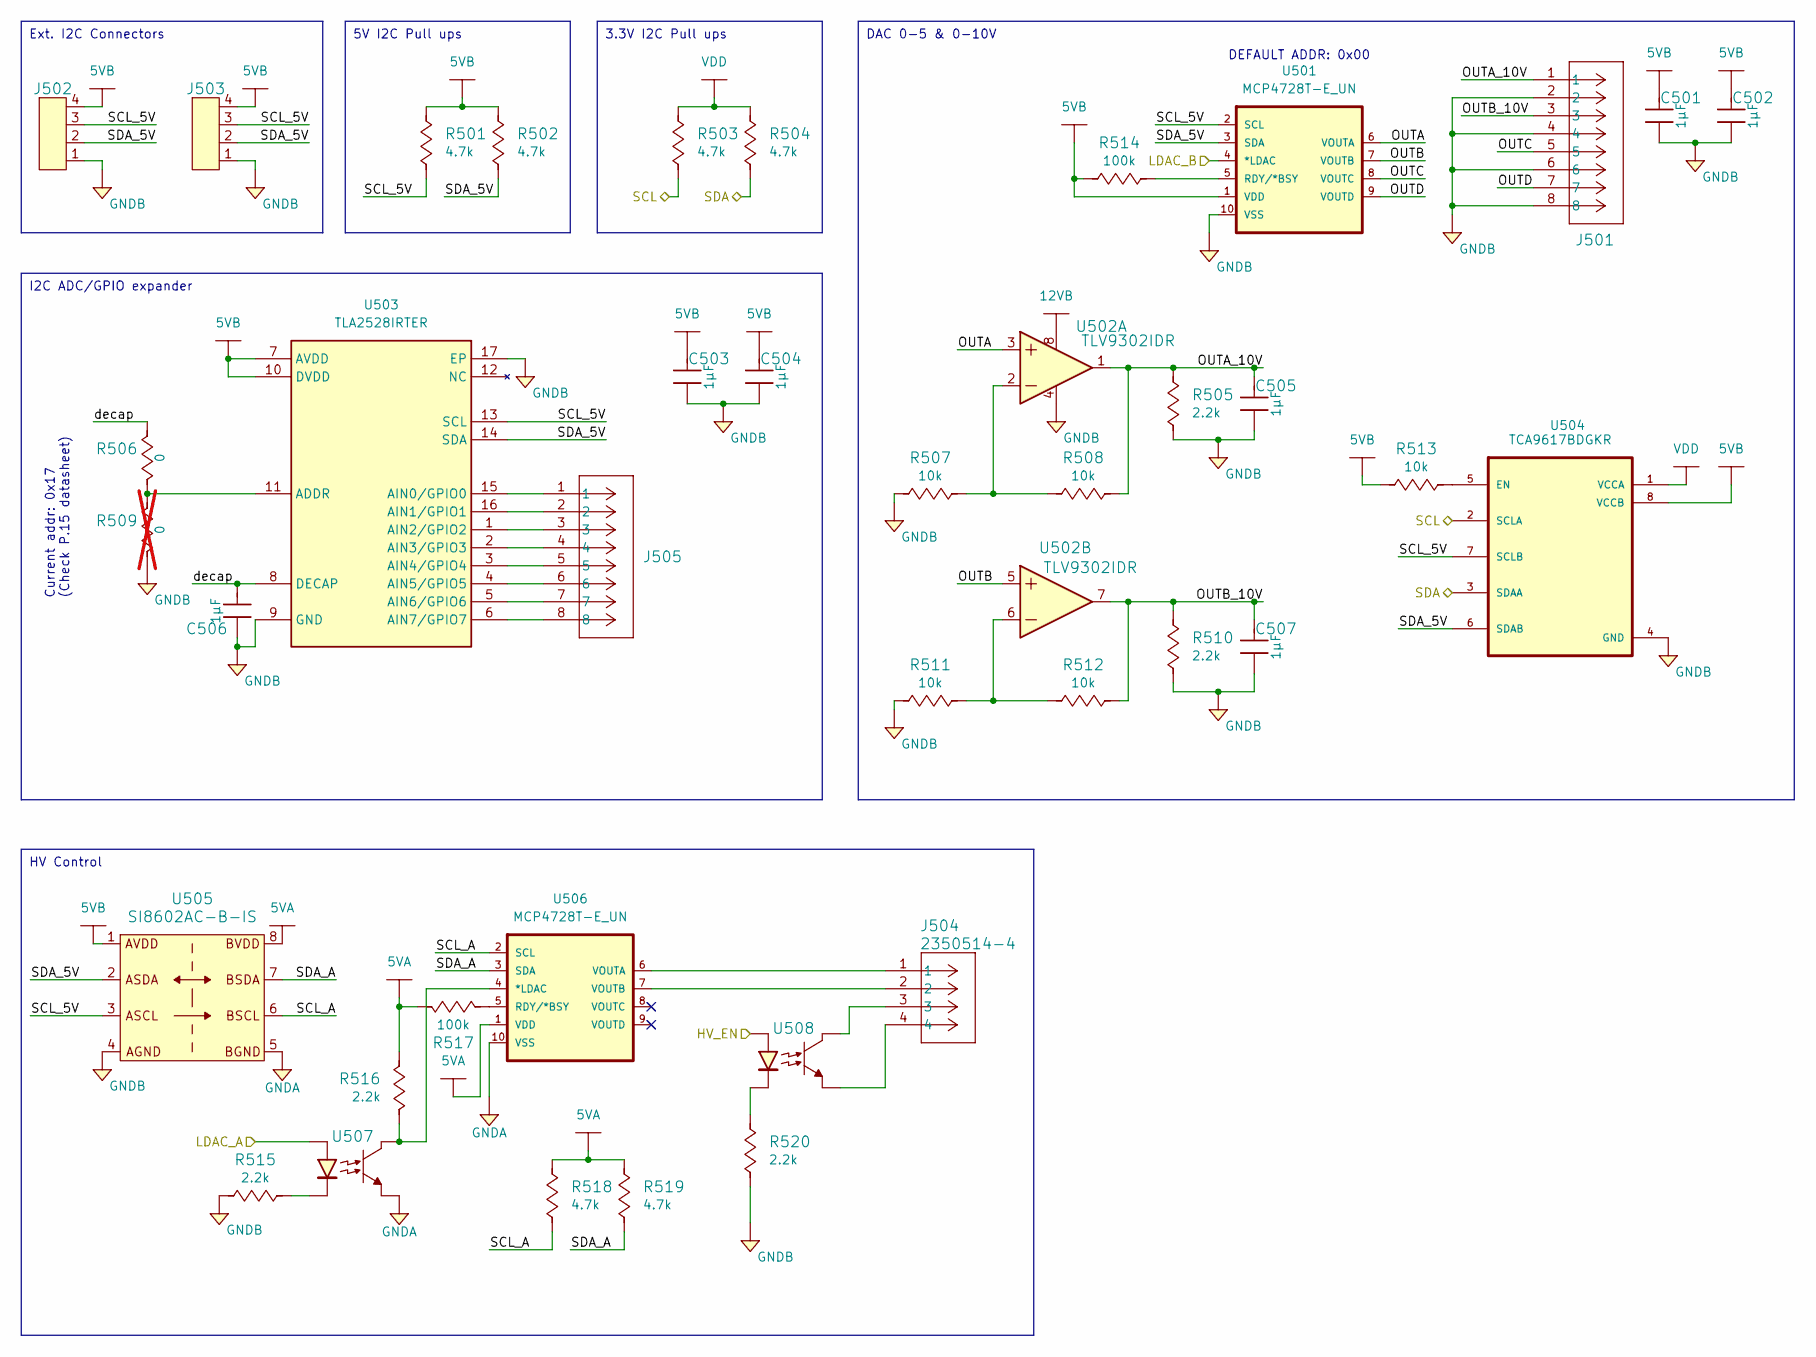
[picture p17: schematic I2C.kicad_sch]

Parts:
C501, C502, C503, C504, C505, C506, C507: 885012107015; C0805; Tolerance (%) ±20%; Voltage Rated (Volt) 25V; Manufacturer Part Number 885012107015
J501, J505: 2350514-8; CONN8_2350514-8_TEC; Manufacturer Part Number 2350514-8
J502, J503: XH-4A connector; XH-4A; Manufacturer Part Number Manufacturer Part Number
J504: 2350514-4; CONN4_1155650000_TEC; Manufacturer Part Number 2350514-4
R501, R502, R503, R504, R518, R519: RC0805JR-074K7L; R0805; Tolerance (%) ±5%; Manufacturer Part Number RC0805JR-074K7L
R505, R510, R515, R516, R520: RC0805JR-072K2L; R0805; Tolerance (%) ±5%; Manufacturer Part Number RC0805JR-072K2L
R506: 0hms_0.5W; R0805; Tolerance (%) 0; Manufacturer Part Number 5106
R507, R508, R511, R512, R513: RC0805JR-0710KL; R0805; Tolerance (%) ±5%; Manufacturer Part Number RC0805JR-0710KL
R509: 0hms_0.5W; R0805; Tolerance (%) 0; Manufacturer Part Number 5106; not fitted
R514, R517: RC0805JR-07100KL; R0805; Tolerance (%) ±5%; Manufacturer Part Number RC0805JR-07100KL
U501, U506: MCP4728T-E_UN; SOP50P490X110-10N; Manufacturer Part Number MCP4728T-E_UN
U502: TLV9302IDR; IC8_TLV9302IDR_TEX; Manufacturer Part Number TLV9302IDR
U503: TLA2528IRTER; QFN50P300X300X80-17N-D; Mouser Part Number 595-TLA2528IRTER
U504: TCA9617BDGKR; SOP65P490X110-8N; Manufacturer Part Number TCA9617BDGKR
U505: SI8602AC-B-IS; SOIC-8; Manufacturer Part Number SI8602AC-B-IS
U507, U508: LTV-816S; 4-SMD; Manufacturer Part Number LTV-816S

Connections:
5VA: R516.1, R517.1, R518.2, R519.2, U505.8 (BVDD), U506.1 (VDD); also elsewhere on the board
5VB: C501.2, C502.2, C503.2, C504.2, J502.4, J503.4, R501.2, R502.2, R513.1, R514.1, U501.1 (VDD), U503.7 (AVDD), U503.10 (DVDD), U504.8 (VCCB), U505.1 (AVDD); also elsewhere on the board
12VB: U502.8; also elsewhere on the board
/I2C/OUTA: U501.6 (VOUTA), U502.3
/I2C/OUTA_10V: C505.2, J501.1, R505.2, R508.2, U502.1
/I2C/OUTB: U501.7 (VOUTB), U502.5
/I2C/OUTB_10V: C507.2, J501.3, R510.2, R512.2, U502.7
/I2C/OUTC: J501.5, U501.8 (VOUTC)
/I2C/OUTD: J501.7, U501.9 (VOUTD)
/I2C/SCL_5V: J502.3, J503.3, R501.1, U501.2 (SCL), U503.13 (SCL), U504.7 (SCLB), U505.3 (ASCL)
/I2C/SCL_A: R518.1, U505.6 (BSCL), U506.2 (SCL)
/I2C/SDA_5V: J502.2, J503.2, R502.1, U501.3 (SDA), U503.14 (SDA), U504.6 (SDAB), U505.2 (ASDA)
/I2C/SDA_A: R519.1, U505.7 (BSDA), U506.3 (SDA)
/I2C/decap: C506.2, R506.1, U503.8 (DECAP)
/IO0: U508.1 (Anode); also elsewhere on the board
/IO21: R504.1, U504.3 (SDAA); also elsewhere on the board
/IO22: R503.1, U504.2 (SCLA); also elsewhere on the board
/IO32: U507.1 (Anode); also elsewhere on the board
/IO33: U501.4 (*LDAC); also elsewhere on the board
GNDA: U505.5 (BGND), U506.10 (VSS), U507.3 (E); also elsewhere on the board
GNDB: C501.1, C502.1, C503.1, C504.1, C505.1, C506.1, C507.1, J501.2, J501.4, J501.6, J501.8, J502.1, J503.1, R505.1, R507.1, R509.2, R510.1, R511.1, R515.2, R520.2, U501.10 (VSS), U502.4, U503.9 (GND), U503.17 (EP), U504.4 (GND), U505.4 (AGND); also elsewhere on the board
unnamed: R507.2, R508.1, U502.2
unnamed: R511.2, R512.1, U502.6
unnamed: R514.2, U501.5 (RDY/*BSY)
unnamed: R506.2, R509.1, U503.11 (ADDR)
unnamed: J505.1, U503.15 (AIN0/GPIO0)
unnamed: J505.2, U503.16 (AIN1/GPIO1)
unnamed: J505.3, U503.1 (AIN2/GPIO2)
unnamed: J505.4, U503.2 (AIN3/GPIO3)
unnamed: J505.5, U503.3 (AIN4/GPIO4)
unnamed: J505.6, U503.4 (AIN5/GPIO5)
unnamed: J505.7, U503.5 (AIN6/GPIO6)
unnamed: J505.8, U503.6 (AIN7/GPIO7)
unnamed: R513.2, U504.5 (EN)
unnamed: R516.2, U506.4 (*LDAC), U507.4 (C)
unnamed: R517.2, U506.5 (RDY/*BSY)
unnamed: J504.1, U506.6 (VOUTA)
unnamed: J504.2, U506.7 (VOUTB)
unnamed: R515.1, U507.2 (Cathode)
unnamed: J504.3, U508.4 (C)
unnamed: R520.1, U508.2 (Cathode)
unnamed: J504.4, U508.3 (E)
VDD: R503.2, R504.2, U504.1 (VCCA); also elsewhere on the board

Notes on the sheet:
3.3V I2C Pull ups
Ext. I2C Connectors
5V I2C Pull ups
HV Control
I2C ADC/GPIO expander
DAC 0-5 & 0-10V
Current addr: 0x17 (Check P.15 datasheet)
DEFAULT ADDR: 0x00

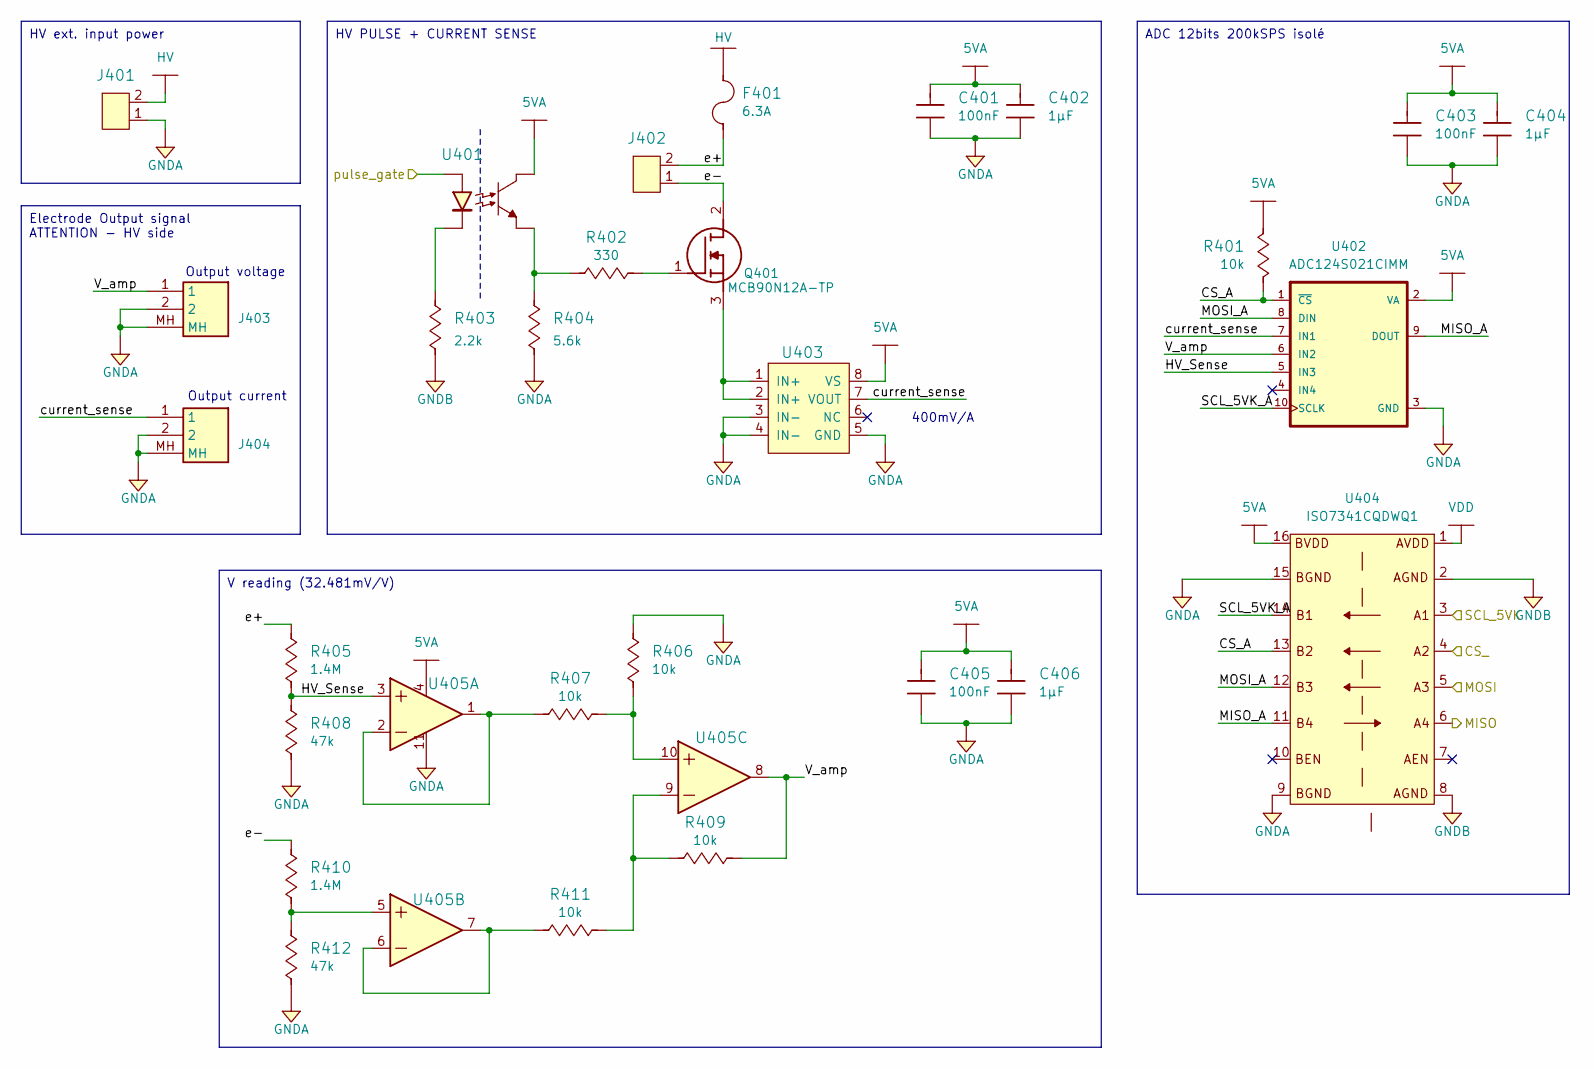
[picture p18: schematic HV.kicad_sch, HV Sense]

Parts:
C401, C403, C405: 885012207098; C0805; Tolerance (%) ±10%; Voltage Rated (Volt) 50V; Manufacturer Part Number 885012207098
C402, C404, C406: 885012207103; C0805; Tolerance (%) ±10%; Voltage Rated (Volt) 50V; Manufacturer Part Number 885012207103
F401: 0698Q6300-01; TE5_395; Current Rating (A) 6.3A; Voltage Rating - DC 140VDC; Manufacturer Part Number 0698Q6300-01
J401, J402: 1935161; Manufacturer Part Number 1935161
J403, J404: RF1-01K-D-00-50-BK-HDW; RF101KD0050; Manufacturer Part Number RF1-01K-D-00-50-BK-HDW
Q401: MCB90N12A-TP; MCB90N12ATP; Manufacturer Part Number MCB90N12A-TP
R401, R406, R407, R409, R411: RC0805JR-0710KL; R0805; Tolerance (%) ±5%; Manufacturer Part Number RC0805JR-0710KL
R402: RC0805JR-07330RL; R0805; Tolerance (%) ±5%; Manufacturer Part Number RC0805JR-07330RL
R403: RC0805JR-072K2L; R0805; Tolerance (%) ±5%; Manufacturer Part Number RC0805JR-072K2L
R404: RC0805FR-075K6L; R0805; Tolerance (%) ±1%; Manufacturer Part Number RC0805FR-075K6L
R405, R410: ERJ-6ENF1404V; R0805; Tolerance (%) 1%; Manufacturer Part Number ERJ-6ENF1404V
R408, R412: RC0805FR-0747KL; R0805; Tolerance (%) ±1%; Manufacturer Part Number RC0805FR-0747KL
U401: LTV-816S; 4-SMD; Manufacturer Part Number LTV-816S
U402: ADC124S021CIMM; SOP50P490X110-10N; Manufacturer Part Number ADC124S021CIMM
U403: TMCS1101A3UQDT; SOIC-8; Manufacturer Part Number TMCS1101A3UQDT
U404: ISO7341CQDWQ1; SOIC-16-wide
U405: MCP6L04T-E/SL; SOIC127P600X175-14N; Manufacturer Part Number MCP6L04T-E/SL

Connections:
5VA: C401.2, C402.2, C403.2, C404.2, C405.2, C406.2, R401.1, U401.4 (C), U402.2 (VA), U403.8 (VS), U404.16 (BVDD), U405.4; also elsewhere on the board
/HV/CS_A: R401.2, U402.1 (~CS), U404.13 (B2)
/HV/HV_Sense: R405.1, R408.2, U402.5 (IN3), U405.3
/HV/MISO_A: U402.9 (DOUT), U404.11 (B4)
/HV/MOSI_A: U402.8 (DIN), U404.12 (B3)
/HV/SCL_5VK_A: U402.10 (SCLK), U404.14 (B1)
/HV/V_amp: J403.1, R409.2, U402.6 (IN2), U405.8
/HV/current_sense: J404.1, U402.7 (IN1), U403.7 (VOUT)
/HV/e+: F401.1, J402.2, R405.2
/HV/e-: J402.1, Q401.2 (D), R410.2
/IO12: U404.6 (A4); also elsewhere on the board
/IO13: U404.5 (A3); also elsewhere on the board
/IO14: U404.3 (A1); also elsewhere on the board
/IO15: U404.4 (A2); also elsewhere on the board
/IO39: U401.1 (Anode); also elsewhere on the board
GNDA: C401.1, C402.1, C403.1, C404.1, C405.1, C406.1, J401.1, J403.2, J403.MH, J404.2, J404.MH, R404.1, R406.1, R408.1, R412.1, U402.3 (GND), U403.3 (IN-), U403.4 (IN-), U403.5 (GND), U404.9 (BGND), U404.15 (BGND), U405.11; also elsewhere on the board
GNDB: R403.1, U404.2 (AGND), U404.8 (AGND); also elsewhere on the board
HV: F401.2, J401.2
unnamed: Q401.1 (G), R402.2
unnamed: Q401.3 (S), U403.1 (IN+), U403.2 (IN+)
unnamed: R406.2, R407.2, U405.10
unnamed: R407.1, U405.1, U405.2
unnamed: R409.1, R411.2, U405.9
unnamed: R410.1, R412.2, U405.5
unnamed: R411.1, U405.6, U405.7
unnamed: R403.2, U401.2 (Cathode)
unnamed: R402.1, R404.2, U401.3 (E)
VDD: U404.1 (AVDD); also elsewhere on the board

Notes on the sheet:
V reading (32.481mV/V)
ADC 12bits 200kSPS isolé
Electrode Output signal ATTENTION - HV side
HV ext. input power
HV PULSE + CURRENT SENSE
Output voltage
Output current
400mV/A

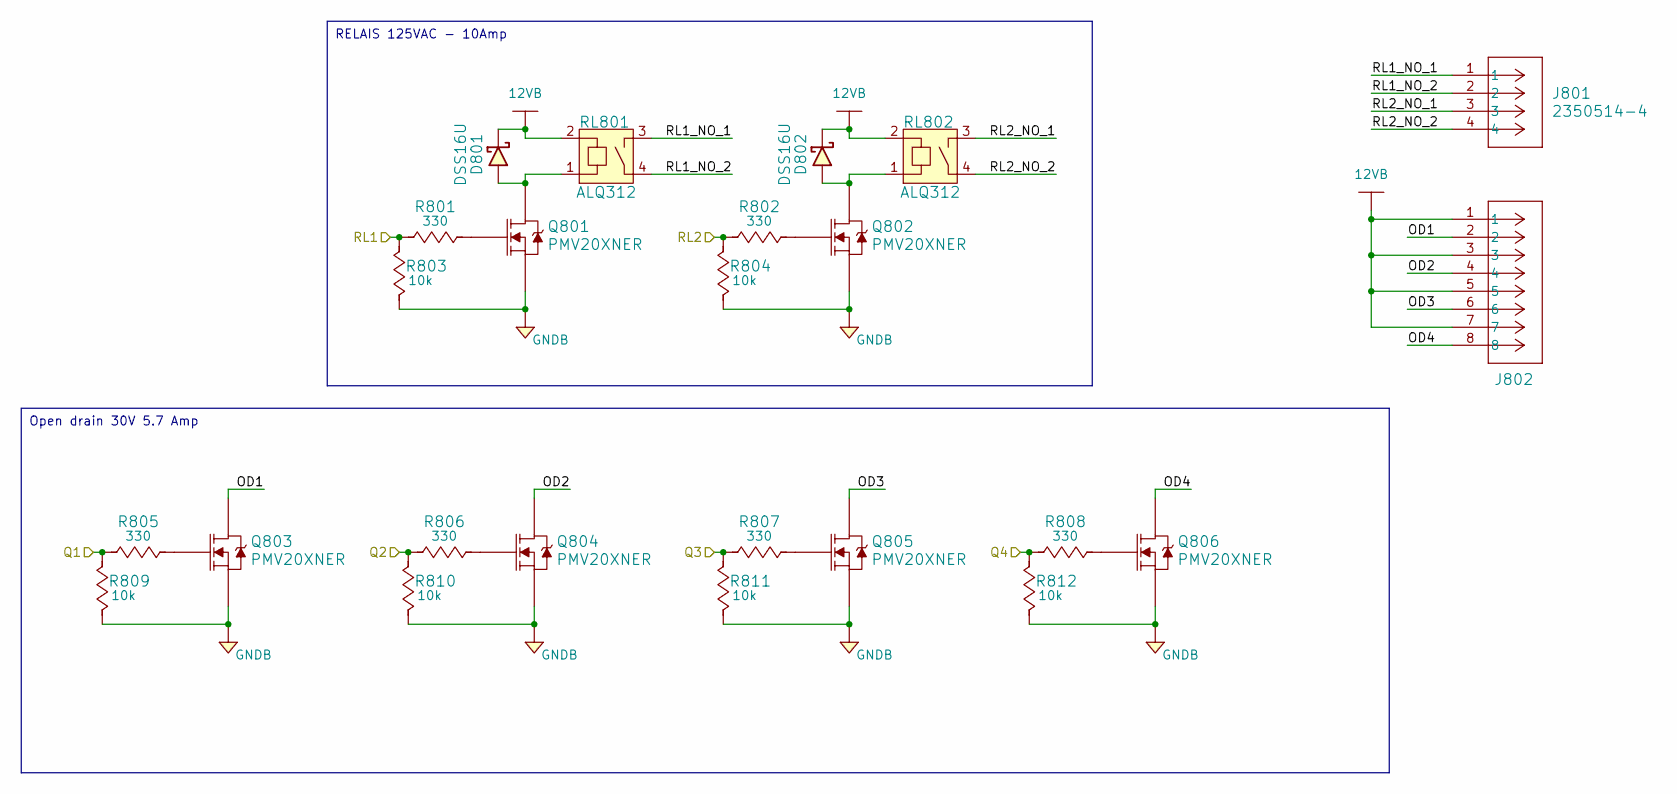
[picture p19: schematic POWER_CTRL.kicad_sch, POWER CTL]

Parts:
D801, D802: DSS16U; SOD-123FL; Manufacturer Part Number DSS16U
J801: 2350514-4; CONN4_1155650000_TEC; Manufacturer Part Number 2350514-4
J802: 2350514-8; CONN8_2350514-8_TEC; Manufacturer Part Number 2350514-8
Q801, Q802, Q803, Q804, Q805, Q806: PMV20XNER; SOT-23-3; Manufacturer Part Number PMV20XNER
R801, R802, R805, R806, R807, R808: RC0805JR-07330RL; R0805; Tolerance (%) ±5%; Manufacturer Part Number RC0805JR-07330RL
R803, R804, R809, R810, R811, R812: RC0805JR-0710KL; R0805; Tolerance (%) ±5%; Manufacturer Part Number RC0805JR-0710KL
RL801, RL802: ALQ312; Manufacturer Part Number ALQ312

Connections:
12VB: D801.1 (Cathode), D802.1 (Cathode), J802.1, J802.3, J802.5, J802.7, RL801.2, RL802.2; also elsewhere on the board
/IO16: R805.1, R809.2; also elsewhere on the board
/IO17: R806.1, R810.2; also elsewhere on the board
/IO18: R807.1, R811.2; also elsewhere on the board
/IO19: R808.1, R812.2; also elsewhere on the board
/IO35: R801.1, R803.2; also elsewhere on the board
/IO36: R802.1, R804.2; also elsewhere on the board
/POWER_CTRL/OD1: J802.2, Q803.3 (D)
/POWER_CTRL/OD2: J802.4, Q804.3 (D)
/POWER_CTRL/OD3: J802.6, Q805.3 (D)
/POWER_CTRL/OD4: J802.8, Q806.3 (D)
/POWER_CTRL/RL1_NO_1: J801.1, RL801.3
/POWER_CTRL/RL1_NO_2: J801.2, RL801.4
/POWER_CTRL/RL2_NO_1: J801.3, RL802.3
/POWER_CTRL/RL2_NO_2: J801.4, RL802.4
GNDB: Q801.2 (S), Q802.2 (S), Q803.2 (S), Q804.2 (S), Q805.2 (S), Q806.2 (S), R803.1, R804.1, R809.1, R810.1, R811.1, R812.1; also elsewhere on the board
unnamed: D801.2 (Anode), Q801.3 (D), RL801.1
unnamed: D802.2 (Anode), Q802.3 (D), RL802.1
unnamed: Q801.1 (G), R801.2
unnamed: Q802.1 (G), R802.2
unnamed: Q803.1 (G), R805.2
unnamed: Q804.1 (G), R806.2
unnamed: Q805.1 (G), R807.2
unnamed: Q806.1 (G), R808.2

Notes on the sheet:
RELAIS 125VAC - 10Amp
Open drain 30V 5.7 Amp

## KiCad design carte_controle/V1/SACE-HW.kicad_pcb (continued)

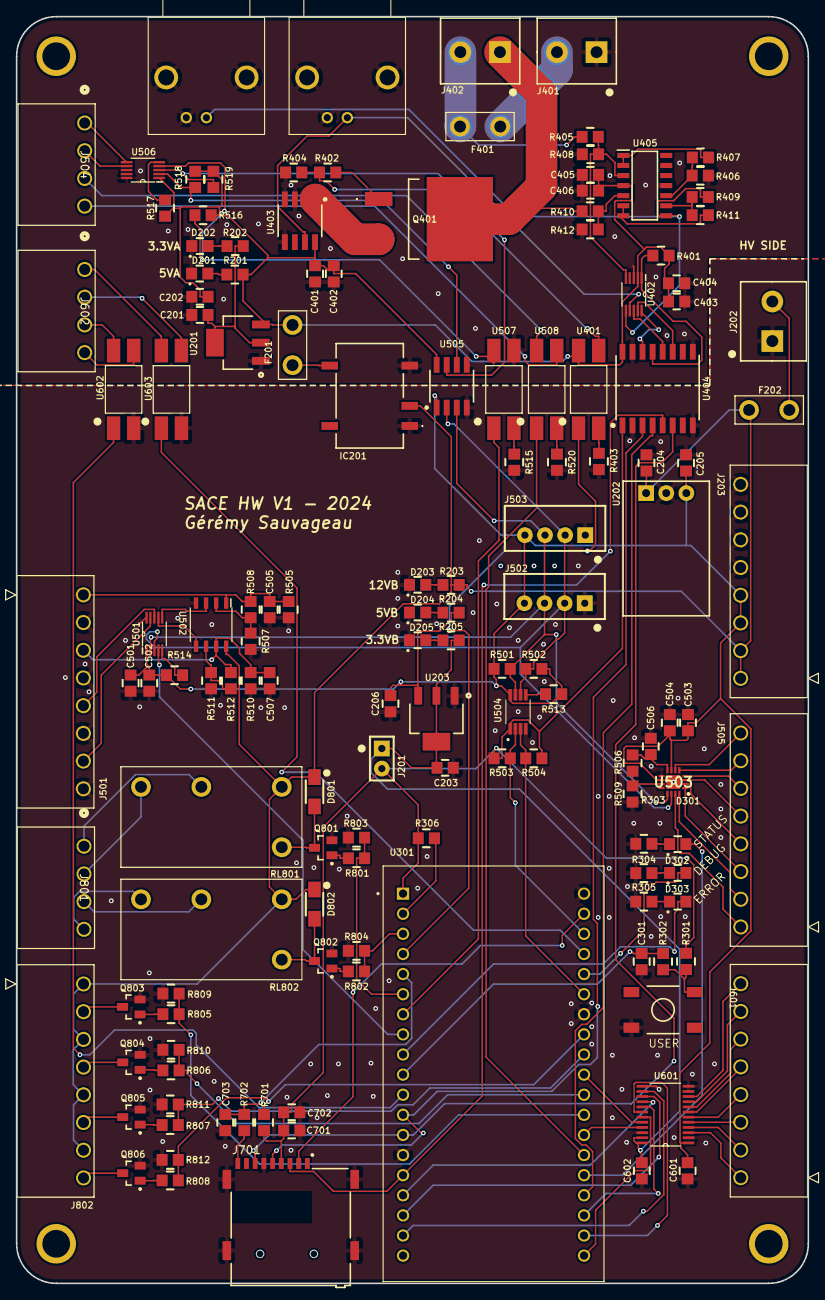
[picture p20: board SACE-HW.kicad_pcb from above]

Board: 2 copper layers, 100.0 x 160.0 mm, 147 parts (0 on the bottom side), 132 nets.

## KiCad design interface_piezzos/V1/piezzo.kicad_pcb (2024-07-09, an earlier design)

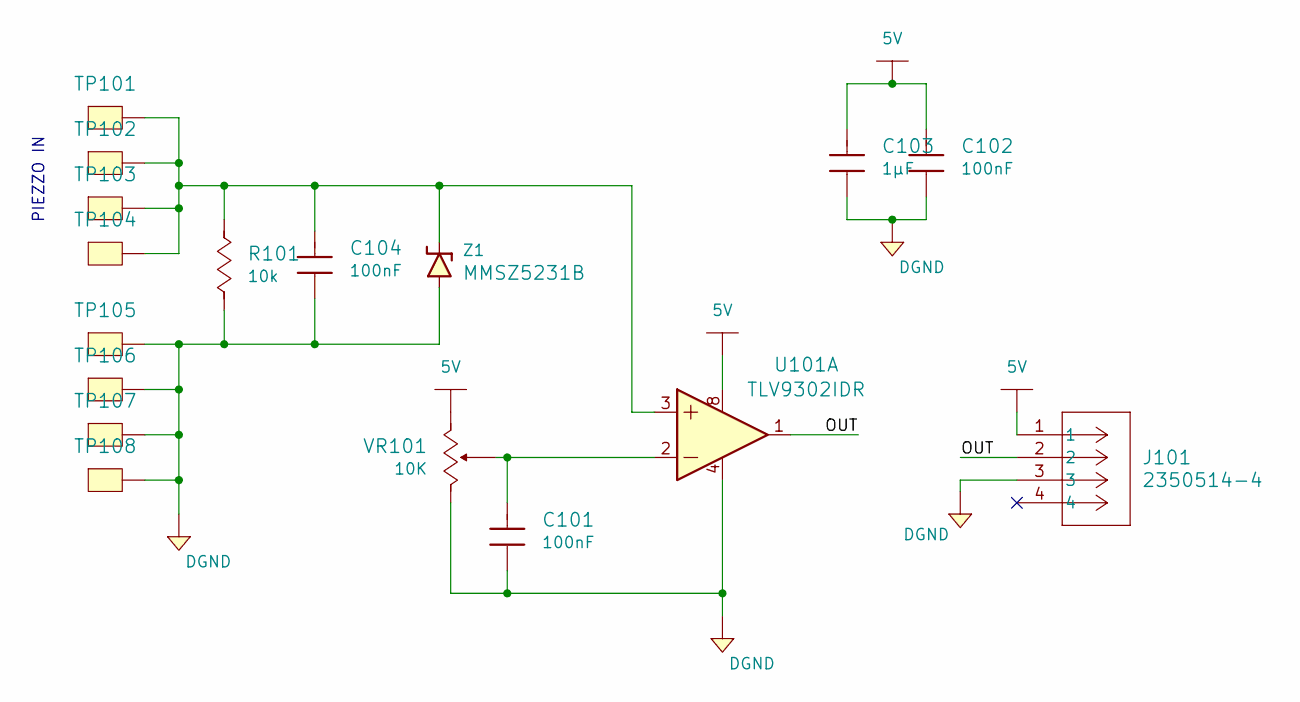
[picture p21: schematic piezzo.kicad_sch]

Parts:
C101, C102, C104: 885012207098; C0805; Tolerance (%) ±10%; Voltage Rated (Volt) 50V; Manufacturer Part Number 885012207098
C103: 885012107015; C0805; Tolerance (%) ±20%; Voltage Rated (Volt) 25V; Manufacturer Part Number 885012107015
J101: 2350514-4; CONN4_1155650000_TEC; Manufacturer Part Number 2350514-4
R101: RC0805JR-0710KL; R0805; Tolerance (%) ±5%; Manufacturer Part Number RC0805JR-0710KL
TP101, TP102, TP103, TP104, TP105, TP106, TP107, TP108: Test_Point_THM; Keystone_5001; Manufacturer Part Number 5001
U101: TLV9302IDR; IC8_TLV9302IDR_TEX; Manufacturer Part Number TLV9302IDR
VR101: 67WR10KLF; 67W; Tolerance (%) ±10%; Manufacturer Part Number 67WR10KLF
Z1: MMSZ5231B; SOD-123FL; Manufacturer Part Number MMSZ5231B-7-F

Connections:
5V: C102.2, C103.2, J101.1, U101.8, VR101.2
/OUT: J101.2, U101.1
DGND: C101.1, C102.1, C103.1, C104.1, J101.3, R101.1, TP105.1 (TP), TP106.1 (TP), TP107.1 (TP), TP108.1 (TP), U101.4, VR101.1, Z1.2 (Anode)
unnamed: C101.2, U101.2, VR101.3
unnamed: C104.2, R101.2, TP101.1 (TP), TP102.1 (TP), TP103.1 (TP), TP104.1 (TP), U101.3, Z1.1 (Cathode)

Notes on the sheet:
PIEZZO IN

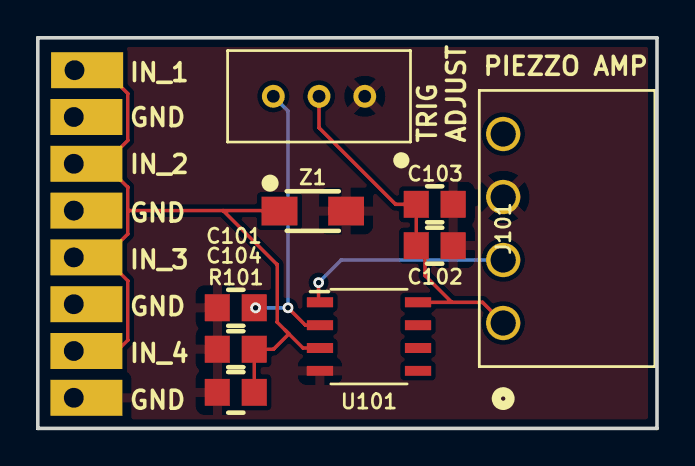
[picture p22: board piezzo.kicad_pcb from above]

Board: 2 copper layers, 34.4 x 21.7 mm, 17 parts (0 on the bottom side), 5 nets.

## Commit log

2024-05-13 nouveau projet + ajout gitignore
    [LV_PSU.kicad_sch, MCU.kicad_sch, PSU.kicad_sch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]
2024-05-13 repo cleanup + modif gitignore
    [PSU.kicad_sch]
2024-05-16 update schematic
    [Acquisition.kicad_sch, HV.kicad_sch, LV_PSU.kicad_sch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]
2024-05-28 modif schématique
    [5V_LOGIC_I2C.kicad_sch, Acquisition.kicad_sch, HV.kicad_sch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]
2024-05-29 update schematique
    [HV.kicad_sch, I2C.kicad_sch, LV_PSU.kicad_sch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]
2024-06-03 finalisation de la schématique
    [5V_OUTPUT.kicad_sch, BOM.csv, HV.kicad_sch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]
2024-06-20 clean up
    [5V_LOGIC_I2C.kicad_sch, 5_12V_OUTPUT.kicad_sch, HV.kicad_sch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]
2024-07-05 parts placement finished
    [5V_OUTPUT.kicad_sch, BOM.csv, HV.kicad_sch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]
2024-07-09 gerber + commande JLC
    [HV.kicad_sch, SACE-HW.kicad_pcb, piezzo.kicad_pcb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]
2024-08-14 un peu d'ordre la dedans
    [carte_controle_BOM.csv, carte_controle_BOM.xlsx, piezzo.kicad_pcb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]
2024-09-09 ajout gitignore + versions
    [5V_OUTPUT.kicad_sch, BOM.csv, HV.kicad_sch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]
